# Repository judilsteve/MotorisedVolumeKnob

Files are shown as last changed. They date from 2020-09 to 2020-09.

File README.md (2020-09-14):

# MotorisedVolumeKnob

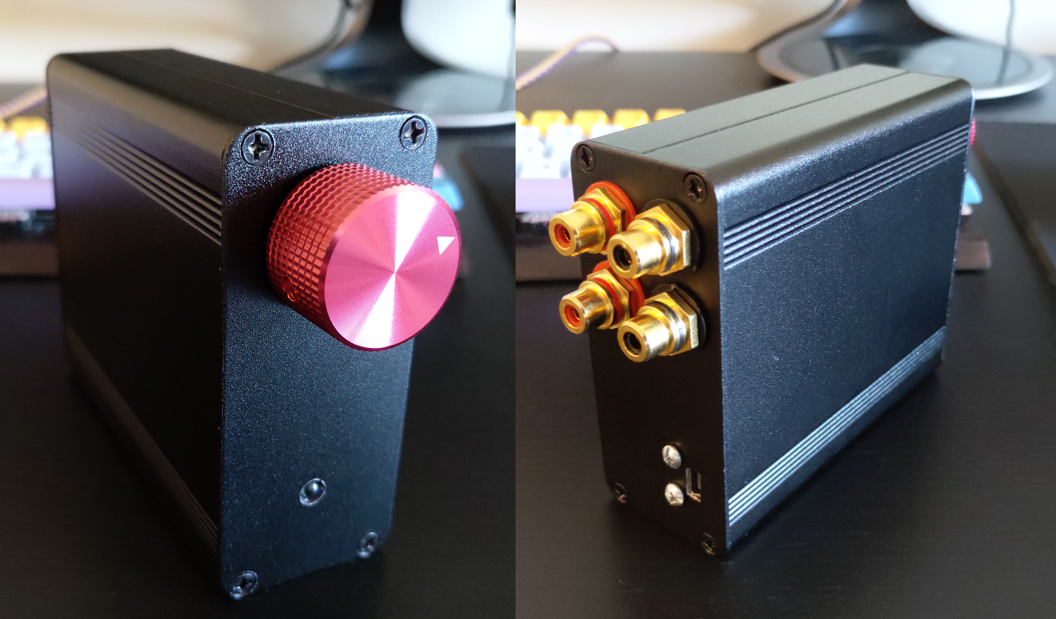
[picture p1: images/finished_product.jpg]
Finished Product


Adjust the volume of your stereo system in style! Turn the knob yourself or sit back and let the IR remote control do it for you: The choice is yours with MotorisedVolumeKnob. Ideal for powered studio monitors (typically sold as individual units, with each speaker having its own amp and volume knob). No more running back and forth between your speakers to match the volume settings every time you need to make an adjustment.

Included in this repo:
 - Parts list (scroll down)
 - STLs for various 3D printable tools/templates/parts to help you build this thing
 - Arduino code to make it all work

## Parts list

I have linked the exact listings that I purchased here, but almost all of these parts are available from many suppliers with stock in lots of different regions. Shop around to find local listings and save on shipping.

 - **[Motorised potentiometer:](https://au.mouser.com/ProductDetail/ALPS/RK16812MG0AF?qs=sGAEpiMZZMtC25l1F4XBUza7emsVrz94iYvX1a0%2Fw%2F8%3D)**
    - **Alternatives:** Just buy this one.
    - **Notes:** Alps is supposedly known for high quality audio potentiometers with smooth actuation and good channel matching. I can confirm that to be the case with these. I wouldn't substitute a different unit here, especially given that other brands don't seem to be much cheaper anyway.

 - **[Enclosure:](https://www.aliexpress.com/item/4000207240540.html)**
    - **Alternatives:** There are too many of these available to list. Plastic ones will be cheaper, or you could even 3D print one quite easily.
    - **Notes:** I wouldn't try to cram these components into anything much smaller than this. If you go with a pre-made enclosure, make a template (STLs available in the repo for the linked enclosure) for drilling pilot holes, and then use a file to bring things to final dimension. It will end up looking much cleaner.

 - **[Knob:](https://www.aliexpress.com/item/32749196662.html)**
    - **Alternatives:** You can use any 6mm shaft knob with a grub screw or a notch (often called "D-Shaft" in listings). 3D printing is also an option here (STL available in the repo).
    - **Notes:** Being solid aluminium, this knob has a nice weighty feel to it and the machining is of very high quality. It also seems to be available in other colours if you're not a fan of red. A lot of the cheaper "aluminium" knobs on sale are actually a thin aluminium cylinder wrapped around an injection moulded plastic core. `[Gap between knob and faceplate] = [potentiometer shaft length] - [knob shaft hole depth] - [faceplate thickness] - [spacer thickness]`. For the parts listed here, that works out to `20mm - \~13.7mm - \~1.2mm - 3mm = \~2mm`. Note that your spacer can be no thicker than 3mm, or else you won't have enough thread on the faceplate side of the shaft for you to thread the locking nut onto.

 - **[RCA sockets:](https://www.aliexpress.com/item/33002834825.html)**
    - **Alternatives:** You can definitely get cheaper, but the gold plating looked super cool. I doubt it makes any audible difference to sound quality, though.
    - **Notes:** You'll need 2 of these 2-packs. Don't solder the positive terminal of these until *after* you have mounted them in the enclosure and put the ground ring in place.

 - **[Motor controller:](https://www.aliexpress.com/item/32925603735.html)**
    - **Alternatives:** Anything based on the L298 chip will work great.
    - **Notes:** Cheap as chips and "brakes" the motor if you set both inputs high at the same time.

 - **[Arduino Nano:](https://www.aliexpress.com/item/32341832857.html)**
    - **Alternatives:** Use any microcontroller you like, but the code here is written for Arduino.
    - **Notes:** You can get away with the cheaper 168P chip for this application, and you don't need the header pins either. Just make sure whichever listing you buy specifies that the bootloader is already installed, or you will be in for a fun time to get it up and running.

 - **[IR Remote:](https://www.aliexpress.com/item/1129167188.html)**
    - **Alternatives:** Basically any IR remote you like. Even one for an old TV you have just lying around. Just make sure you get a receiver with a matching carrier frequency. The code in this repo only works with [NEC protocol](https://www.sbprojects.net/knowledge/ir/nec.php) remotes, but Arduino libraries like [IRLib2](https://github.com/cyborg5/IRLib2/tree/master/IRLib2) should have you covered for other protocols.
    - **Notes:** This one came with battery, which is great. It uses the NEC protocol, which is widely supported by many Arduino libraries. It also includes a matching demodulating receiver, but I found that the receiver would miss repeat pulses and the motor would stutter, so I ended up swapping in a more expensive receiver (see below).

 - **[IR Receiver:](https://www.jaycar.com.au/5mm-infrared-receiver/p/ZD1952)**
    - **Alternatives:** Beware cheap receivers. The cheap ones I tried worked fine for about one second of continuous button-holding and then started to miss IR pulses, causing the motor to stutter. The remote above requires a receiver tuned to a 37.9kHz (often listed as 38kHz) carrier frequency.
    - **Notes:** You can get larger modules that combine multiple receivers to allow your remote to work from wider angles and longer distances.

## STLs

See the "STLs" folder for:

 - Printable templates to help you drill/file holes for the aluminium enclosure in the parts list above
 - Spanners for tightening the panel mount RCA jacks (you'll need two of these, one for each side)
 - A spacer for the potentiometer shaft to move the knob as close as possible to the faceplate
 - A mounting bracket for the Arduino Nano

## Arduino code

### Usage and Configuration

In `setup()`, ensure that your pins are configured correctly:

```c++
int const IR_RECV_PIN = 2;
int const VOLUME_UP_PIN = 4;
int const VOLUME_DOWN_PIN = 3;

void setup()
{
    pinMode(IR_RECV_PIN, INPUT);
    pinMode(VOLUME_UP_PIN, OUTPUT);
    pinMode(VOLUME_DOWN_PIN, OUTPUT);
}
```

You will need to attach an IRReceiver to the pin-level interrupt for your desired digital input pin using the templated singleton:

```c++
// Most IR demodulators that I've come across invert the demodulated signal
// That is, the input pin goes LOW when the receiver is detecting a carrier pulse
// Therefore, you likely want to set the 'inverted' parameter here to true
auto & receiver = InputPinIrReceiver<IR_RECV_PIN>::Attach(/*inverted:*/true);
```

Then create a motor state machine that reads your receiver, supplying an appropriate configuration:

```c++
auto motorStateMachine = VolumeMotorStateMachine(
    receiver,
    VolumeMotorConfig{
        // IR code for the remote button that you want to map to volume +
        .VolumeUpCode = 0xFFA857,
        // IR code for the remote button that you want to map to volume -
        .VolumeDownCode = 0xFFE01F,
        // Output pin that, if set HIGH, will drive the motor to increase the volume
        .VolumeUpPin = 4,
        // Output pin that, if set HIGH, will drive the motor to decrease the volume
        .VolumeDownPin = 3,
        // Duration that both output pins will be set HIGH to "brake" the motor when it
        // is set to idle. See here for more info: https://en.wikipedia.org/wiki/H-bridge#Operation
        .BrakeDurationMicros = 100UL * 1000UL,
        // Duration that the state machine will wait between IR remote packets before
        // assuming that the remote button has been released and stopping the motor
        // Note: In the standard NEC protocol, repeat pulses are spaced 110ms apart,
        // so setting the timeout to a value less than this will likely cause the motor
        // to stutter
        .MovementTimeoutMicros = 120UL * 1000UL
    });
```

Finally, place a call to `motorStateMachine.tick()` at the top level of your `loop()` function:

```c++
void loop()
{
    motorStateMachine.Tick();
}
```

### Troubleshooting

If you find that your volume motor works fine in short bursts, but begins to stutter or stalls when the button is held for longer periods of time, you most likely have a poor quality IR receiver/demodulator. I experienced these issues with a cheap demodulator that was bundled with my remote control. Upgrading to a higher quality demodulator fixed the issue.

### Motivation

I was originally going to use [IRremote](https://github.com/z3t0/Arduino-IRremote) or [IRLib2](https://github.com/cyborg5/IRLib2) for this project, however I found that no matter how I configured my receiver, the remote control for my Panasonic air conditioner would interfere with it, causing the IR receiver object to return a blank code every time I checked for a code until the Arduino was rebooted. So I built the simplest possible NEC protocol decoder that I could, to make my receiver resilient against interference. With my library, the air conditioner remote control is ignored as desired.

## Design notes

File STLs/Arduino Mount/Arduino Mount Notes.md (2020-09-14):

Your Arduino Nano should friction fit into the mount. Wrap a cable tie around it to clamp the jaws around the Arduino, and then use some self-tapping sheet metal screws (I used 4Gx9mm) to attach the mount to the rear faceplate of your enclosure.

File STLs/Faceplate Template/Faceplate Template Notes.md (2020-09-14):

This is designed as a template that you can screw in on top of the enclosure in the parts list to assist you in drilling/filing the holes for the various components.
However, if you increased the thickness you could use it as part of a fully 3D printed enclosure.

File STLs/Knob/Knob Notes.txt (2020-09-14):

Fully 3D printable knob with some nice grippy bits on it. Should sit perfectly flush against a 1.2mm faceplate when using the potentiometer in the parts list, without requiring a spacer.

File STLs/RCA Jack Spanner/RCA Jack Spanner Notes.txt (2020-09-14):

Use these to tighten the nuts on your panel mount RCA jacks. You'll need to print two: One to hold the part of the jack that faces the outside, and another to turn the nut on the inside.

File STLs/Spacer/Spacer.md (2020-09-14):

This spacer is designed to go between the potentiometer's front face and the faceplate of the enclosure. The spacer reduces the gap between the knob and the faceplate on the outside of the enclosure. It is 3mm thick in the file here, which is as thick as you can print it before you run out of thread on the outside of the faceplate for securing the locking nut around the potentiometer shaft. If you need a thinner spacer, you can scale it in the z direction with your slicer software.

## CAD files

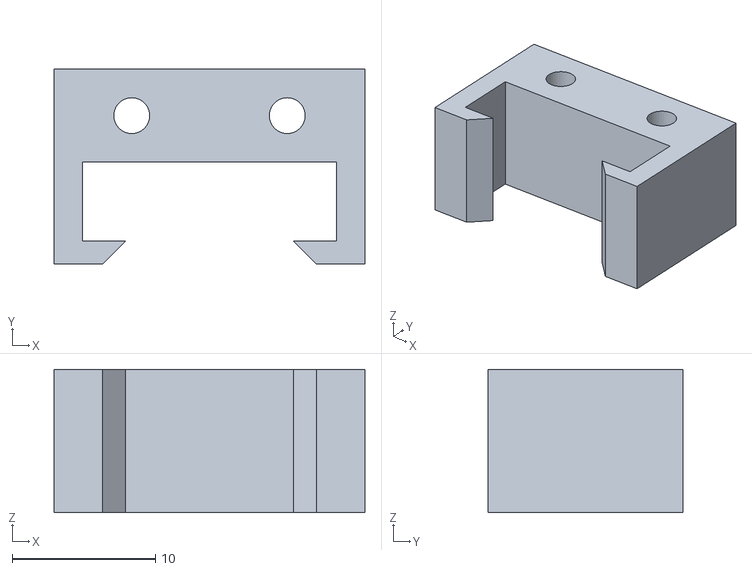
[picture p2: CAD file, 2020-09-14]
STLs/Arduino Mount/Arduino Mount.STL
21.7 x 13.6 x 10.0

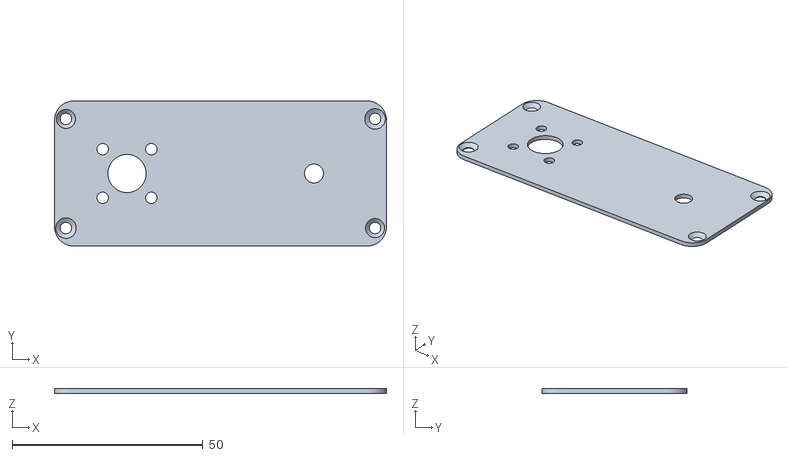
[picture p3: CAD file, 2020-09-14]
STLs/Faceplate Template/Faceplate Template.STL
87.0 x 38.0 x 1.20

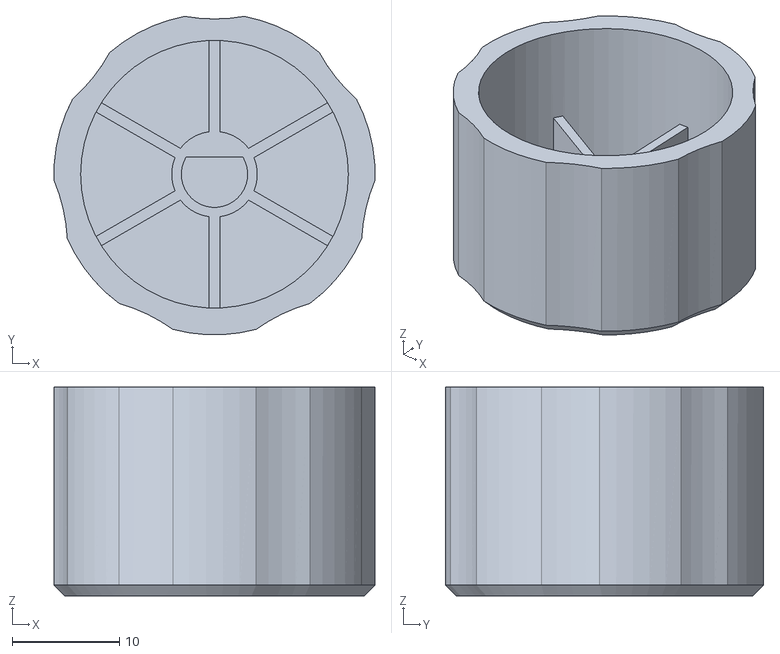
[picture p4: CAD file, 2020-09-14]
STLs/Knob/Knob.STL
30.0 x 29.7 x 19.5

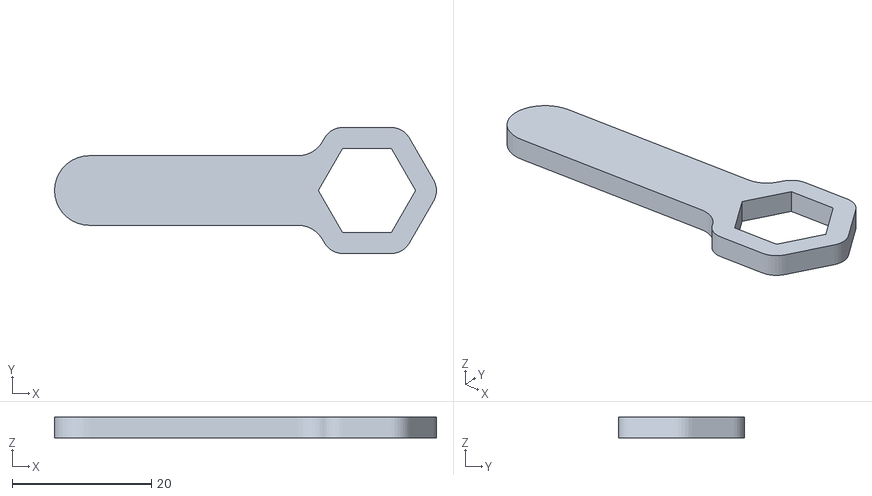
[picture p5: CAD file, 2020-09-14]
STLs/RCA Jack Spanner/RCA Jack Spanner.STL
54.9 x 18.1 x 3.00

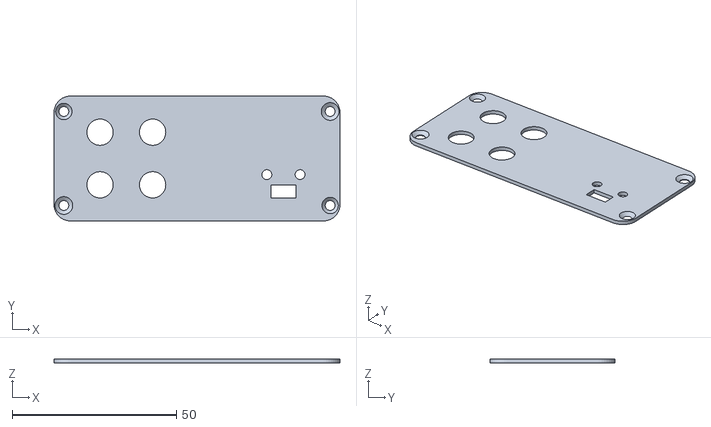
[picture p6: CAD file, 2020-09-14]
STLs/Rear Plate Template/Rear Plate Template.STL
87.0 x 38.0 x 1.20

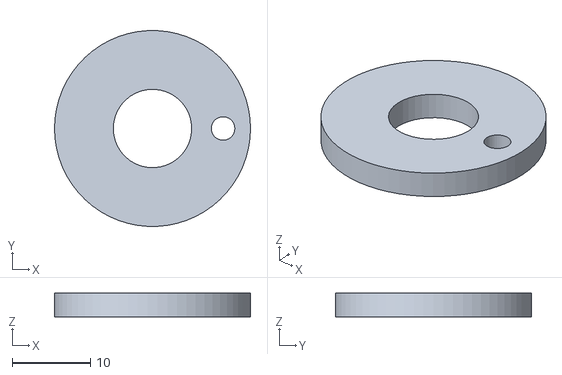
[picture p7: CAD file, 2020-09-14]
STLs/Spacer/Spacer.STL
25.0 x 25.0 x 3.00

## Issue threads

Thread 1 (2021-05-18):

Schematic

bitshitter, 2021-05-18:
Is there a schematic available to see how it should be wired up? I had a look through the files and didn't see anything and the pictures are all of the closed case.

judilsteve, 2021-05-19:
I haven't made any schematics myself, but you can piece together the circuit for the signal path from the "Terminal Layout / Circuit Diagram" section of the potentiometer datasheet [here](https://au.mouser.com/datasheet/2/15/RMP_RK16-1370992.pdf).

I wired my potentiometers as [voltage dividers](https://learn.sparkfun.com/tutorials/voltage-dividers/all), which means that the minimum volume position is an open circuit on the output (total mute). I have not experimented with wiring the potentiometer in series with the signal path. You might be able to get a more linear-sounding attenuation curve that way (at the expense of not being able to entirely mute the output).

The wiring for the motor controlller and IR receiver should be fairly self-explanatory: Follow the silkscreen markings for Vcc/GND, and wire the signal pins to whichever digital inputs/outputs on your microcontroller are most convenient. Then, adjust the pin numbers in the Arduino sketch to match.

bitshitter, 2021-05-19:
Great thanks. I'll give it a go and maybe even create a schematic and post it if I get round to it.

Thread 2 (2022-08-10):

Adding a Mute (speaker) relay

ayush-tanna, 2022-08-10:
Hi, Thanks for this wonderful effort.
I have added code to make a pin control a speaker relay to act as a mute switch from the remote. This relay should remain closed on power on and when required opened with a remote button - the same acting a toggle to switch it back on. Also when muted either of the Volume Up or Down buttons should close the relay.
[iR-Mute.zip](https://github.com/judilsteve/MotorisedVolumeKnob/files/9300660/iR-Mute.zip)
Unfortunately it is not working. Please help.

judilsteve, 2022-08-11:
You're on the right track, but I don't think you've quite grokked how the `State<T>` classes work. Here's a simplified model of the state machine (with your mute state added). There's a couple transitions here that I haven't bothered to draw (e.g. jumping straight from the braking state to the vol-/vol+ state) but it's detailed enough for explanatory purposes:

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

If you're not familiar with state machines, they are basically just [directed graphs](https://en.wikipedia.org/wiki/Directed_graph). The vertices (circles) are the possible states that the machine can be in (idle, volume increasing, braking, muted, etc), and the edges (arrows) are the possible transitions between those states. State machines typically operate in discrete cycles known as "ticks". During each tick, the state machine decides (based on what's going on in the world and what state it is currently in) whether it will move to a different state, or stay in the same state.

In my representation of a state machine, each state is represented by a subclass of the `State` class. Every tick, the current state's `Tick` function is called. Whatever is returned by that function will be the new state of the state machine. This is certainly not the only way to implement a state machine, and I'm not even sure it's a *good* way to implement a state machine, but it seemed like a reasonable enough idea at the time.

Anyway, let's look at the `Tick` function for `IdleMotorState`:

```c++
MotorStateId const Tick(unsigned long const)
{
    IrPacket packet;
    if (irReceiver.TryGetPacket(packet) && !packet.IsRepeat)
    {
        if (packet.Code == config.VolumeUpCode) return VOLUME_INCREASING;
        else if (packet.Code == config.VolumeDownCode) return VOLUME_DECREASING;
    }
    return IDLE;
}
```

This function defines the logic that we should follow while we are in the idle state. What it says is:

 - If the volume up button was pressed, move to the `VOLUME_INCREASING` state
 - If the volume down button was pressed, move to the `VOLUME_DECREASING` state
 - Otherwise, stay in the `IDLE` state.

In essence, each of the return values inside a state's Tick function represents one of the edges *leaving* that state's vertex in the directed graph (note the colour key next to each return value):

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

When the return value is the same state as the one the state machine is currently in, we can think of this as an "implied" edge that loops back around onto the same vertex.

Let's take a look at the `Tick` function that you've written for your new `SpeakerMuteState`:

```c++
MotorStateId const Tick(unsigned long const)
{
    IrPacket packet;
    if (irReceiver.TryGetPacket(packet) && !packet.IsRepeat)
    {
        if (packet.Code == config.MuteCode) return MUTE;
    }
    return MUTE;
}
```

Essentially, you've built this state machine:

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

Because you haven't modified any of the existing state functions to return `MUTE`, there's no way to ever enter the muted state. Additionally, because your `SpeakerMuteState`'s Tick function never returns anything other than `MUTE`, there's no way to ever *leave* the mute state once you get there.

Closed 2022-08-11.

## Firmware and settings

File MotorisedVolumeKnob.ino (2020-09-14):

#include "IrReceiver.h"
#include "VolumeMotorStateMachine.h"

using namespace IrReceiverUtils;
using namespace VolumeMotorUtils;

int const IR_RECV_PIN = 2;
int const VOLUME_UP_PIN = 4;
int const VOLUME_DOWN_PIN = 3;

void setup()
{
    pinMode(IR_RECV_PIN, INPUT);
    pinMode(VOLUME_UP_PIN, OUTPUT);
    pinMode(VOLUME_DOWN_PIN, OUTPUT);
}

auto & receiver = InputPinIrReceiver<IR_RECV_PIN>::Attach(/*inverted:*/true);

auto motorStateMachine = VolumeMotorStateMachine(
    receiver,
    VolumeMotorConfig
    {
        .VolumeUpCode = 0xFFA857,
        .VolumeDownCode = 0xFFE01F,
        .VolumeUpPin = VOLUME_UP_PIN,
        .VolumeDownPin = VOLUME_DOWN_PIN,
        .BrakeDurationMicros = 100UL * 1000UL,
        .MovementTimeoutMicros = 120UL * 1000UL
    });

void loop()
{
    motorStateMachine.Tick();
}

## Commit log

2020-07-08 Adding readme. Adding input invert parameter.
    [MotorisedVolumeKnob.ino]
2020-07-27 Make volume motor state machine configurable, update demo sketch to use it.
2020-07-27 Update readme and code sample
2020-09-14 Fix bug caused by anonymous struct literal
    [MotorisedVolumeKnob.ino]
2020-09-14 Add parts list to readme, add STLs.
    [Arduino Mount.STL, Faceplate Template.STL, Knob.STL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]
